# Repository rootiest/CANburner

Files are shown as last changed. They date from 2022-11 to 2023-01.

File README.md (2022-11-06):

# CANBurner

This Project originated from the idea of making the swapping process of the Stealthburner front easier.

CANBurner is a PCB design, that works in cooperation with Hartk's 2pc PCB design.

It consists of a front-part and our adapted CANBurner
The CANBurner is the connection PCB between an EBB36 or EBB42 or any CAN module and the movable front PCB.
over the course of the revisions functions were added and the design was changed. 

# Changelog:
## Rev 1.0 (initial design; tested) 19.10.2022

- adapted the footprint of Hartk's Backplate to fit for our purpose
- JST-XH connectors for 2x fans (Hotend and Part-cooling) and 1x LED added
- 2x3 angled pin header to connect to the front PCB 
- simple wire paths over the board
- a through-hole design for easy soldering at home

first tests by André show, that the design fits perfectly on the CW2 extruder. dimensions reach barely past the motor backplate. 
THD components don't collide with each other or the SB. Functions are fully present and the JST connectors make swapping cables easy.
Space can be used more effectively. JST is not as important, the cables can be soldered directly on the Board.

## Rev 2.0 04.11.2022

- Name CANBurner was suggested by rootiest
- added one more JST-XH for I2C connection
- added 2x4 angled pin header 
- placement of connectors were changed
- added Voron Logo 
- minor cleanup of traces and text

## Rev 2L 05.11.2022

- added Neopixel SMD light as status LED
- changed traces
- added voltage test-points for 24V, 5V and GND
- added "rootiest"-Logo

## Rev 3

- fully changed plug design
- one 8 pin JST-PH to connect to CAN board
- 4 pin socket header to allow for direct I2C connection
- SMD LED and solder traces to skip LED when its ot used

## Credits

CANBurner is a collaboration between [Chris Laprade](https://github.com/rootiest/) and [André Bernbrich](https://github.com/Peviox)

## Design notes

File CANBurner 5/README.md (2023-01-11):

<!--
 Copyright (C) 2022 Chris Laprade (chris@rootiest.com)
 
 This file is part of CANburner.
 
 CANburner is free software: you can redistribute it and/or modify
 it under the terms of the GNU General Public License as published by
 the Free Software Foundation, either version 3 of the License, or
 (at your option) any later version.
 
 CANburner is distributed in the hope that it will be useful,
 but WITHOUT ANY WARRANTY; without even the implied warranty of
 MERCHANTABILITY or FITNESS FOR A PARTICULAR PURPOSE.  See the
 GNU General Public License for more details.
 
 You should have received a copy of the GNU General Public License
 along with CANburner.  If not, see <http://www.gnu.org/licenses/>.
-->

# CANBurner 5

## What is it?

CANBurner is an adaptation of hartk's 2-piece StealthBurner PCB.

CANBurner adapts this concept for use on printers with a CANbus toolhead like the BigTreeTech EBB or the Mellow FLY-SHT.

## What is new in v5?

Version 5 includes all of the features from previous versions.

In addition, v5:

- Fixes an issue with the status LED placement/rotation. It should now be compatible with most common neopixel chips of the appropriate size
  
- Cleans up some trace and mask positioning for better fabrication results

- Adds clearer silkscreen labeling for the LED and Resistor (and accompanying bypasses)

- Re-introduces curvy traces!

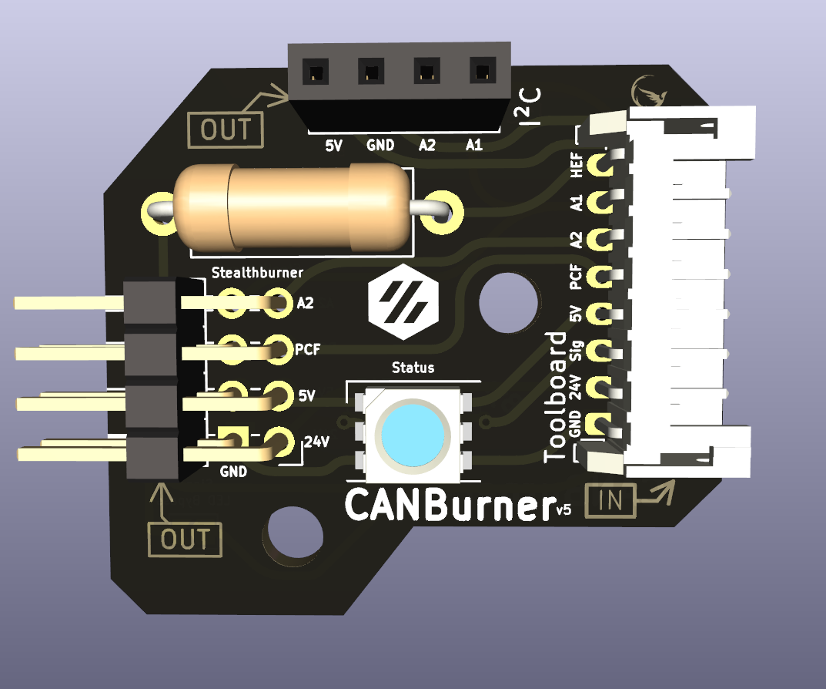
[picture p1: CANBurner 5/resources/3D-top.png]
3D Top View


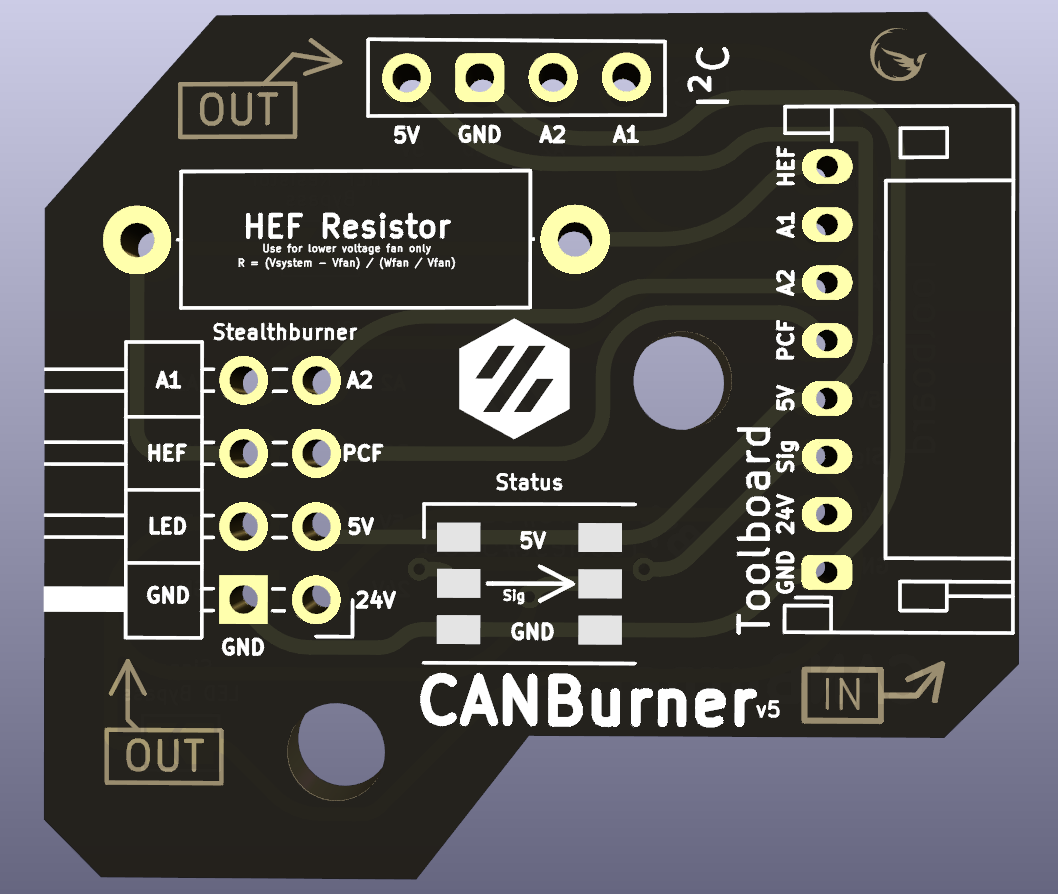
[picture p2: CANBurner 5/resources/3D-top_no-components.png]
3D Top No Components


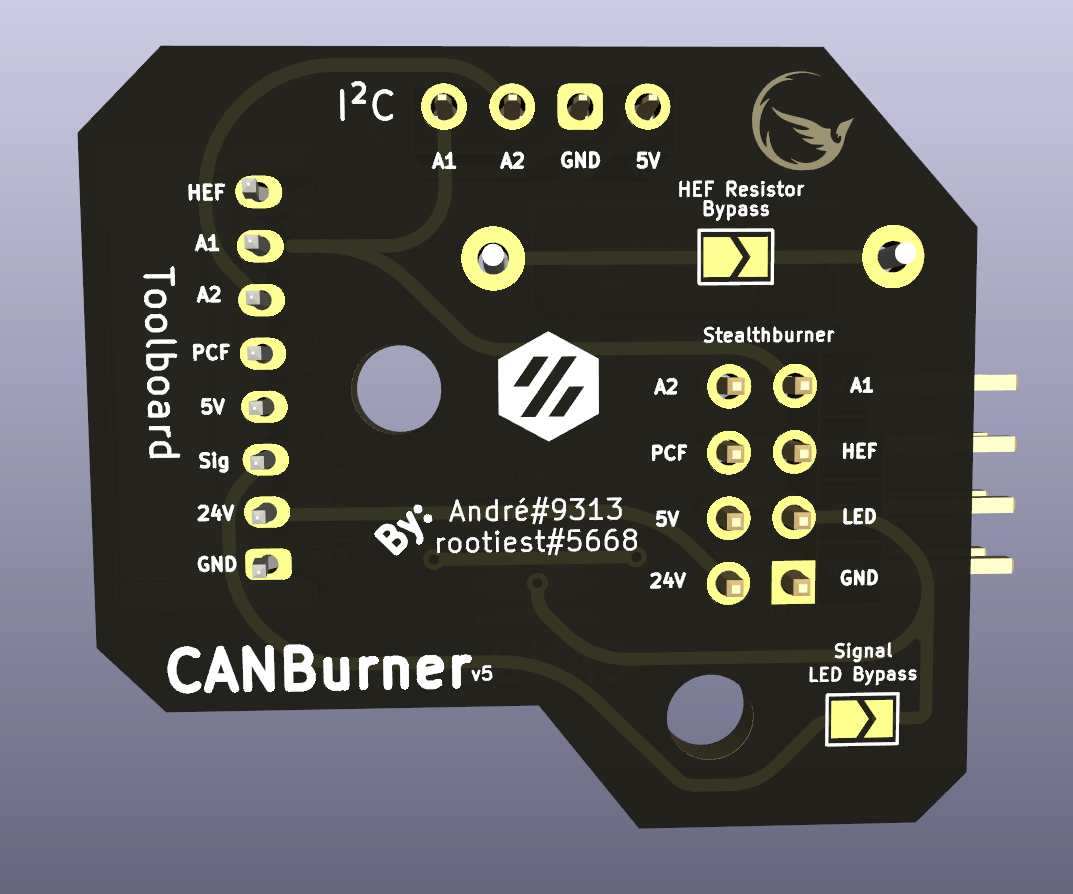
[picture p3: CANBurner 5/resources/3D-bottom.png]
3D Bottom View


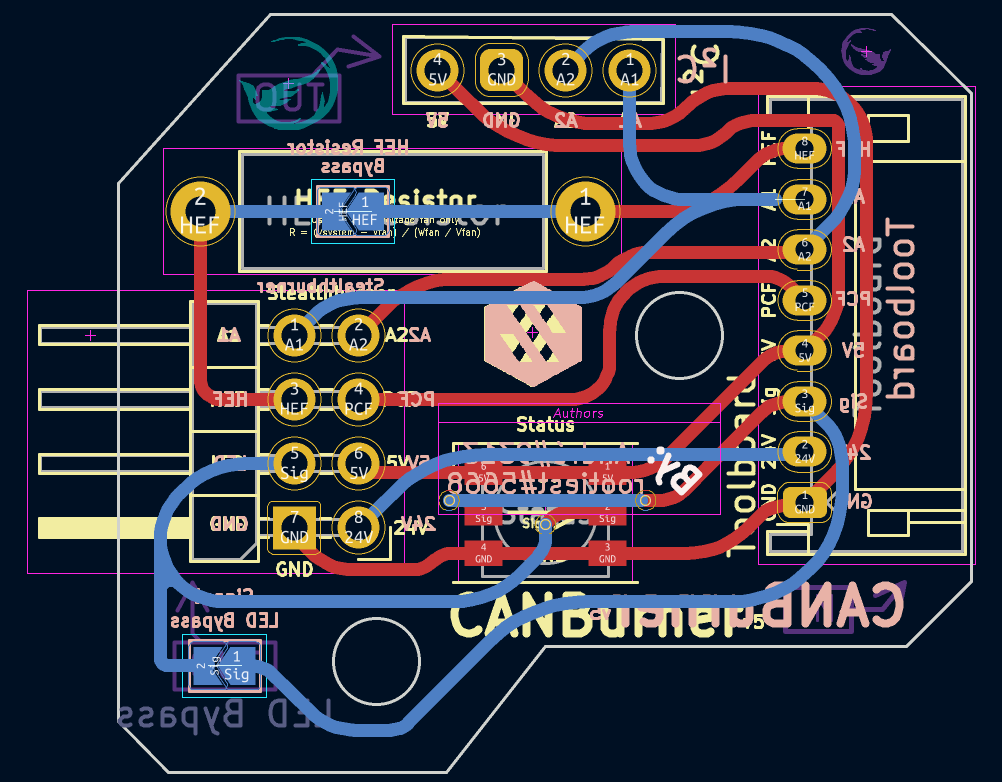
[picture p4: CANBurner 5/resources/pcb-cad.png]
PCB Layout


## How does it work?

Just like [hartk's boards](https://github.com/hartk1213/MISC/tree/main/PCBs/Stealthburner_Toolhead_PCB) do!

[Watch this video](https://www.youtube.com/watch?v=PCIwZRPYMZ8)

Instead of attaching a ribbon, our board just connects to the corresponding pins on your CANbus toolboard.

Its purpose is to act as a "quick-connect" bridge that allows you to remove the stealthburner without disconnecting and reconnecting several connectors for components like fans and LEDs.

The pins will align and connect when you attach the stealthburner front to the extruder.

CANBurner v5 pcb

The images below show an older version but the installation is the same:

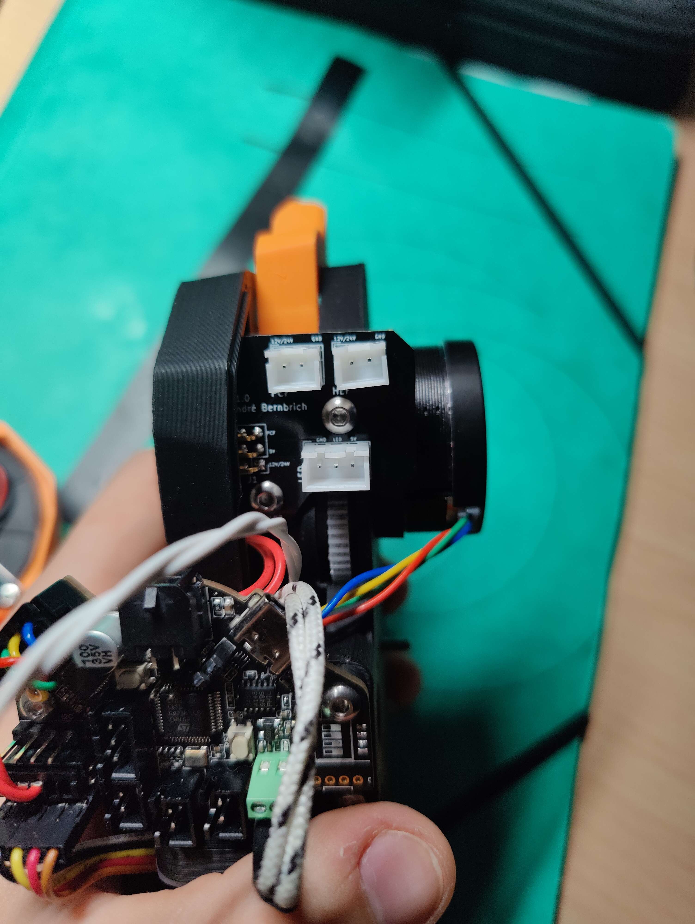
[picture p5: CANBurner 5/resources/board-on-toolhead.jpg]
CANBurner on toolhead


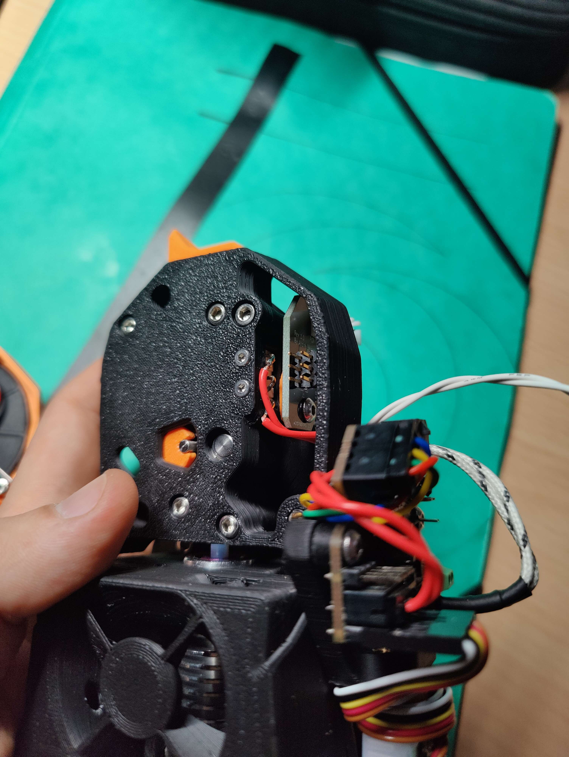
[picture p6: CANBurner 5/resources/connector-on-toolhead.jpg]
CANBurner quick-connect pins


## Credits

CANBurner is a collaboration between [Chris Laprade](https://github.com/rootiest/) and [André Bernbrich](https://github.com/Peviox)

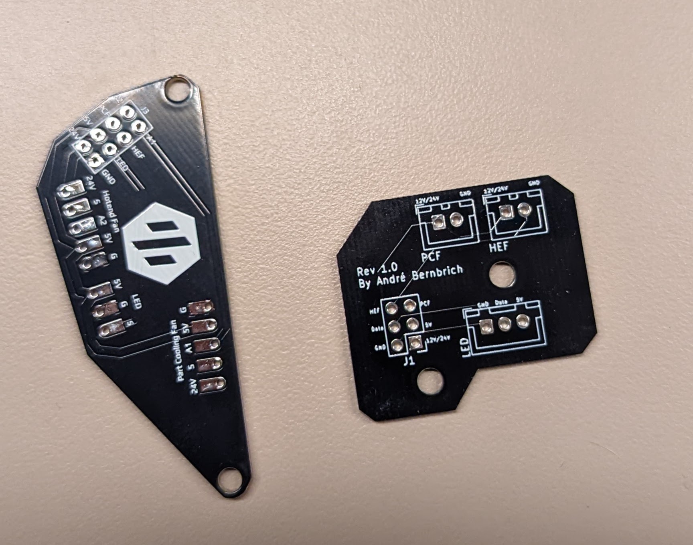
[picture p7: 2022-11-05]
CANBurner 5/resources/pcb-v1.jpg

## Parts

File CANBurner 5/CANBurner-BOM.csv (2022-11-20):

Id | Designator | Package | Quantity | Designation | Supplier and ref
1 | I²C | PinSocket_1x04_P2.54mm_Vertical | 1 | i2C Addon
2 | Status | LED_WS2812_PLCC6_5.0x5.0mm_P1.6mm | 1 | LED_WS2812_PLCC6_5.0x5.0mm_P1.6mm
3 | Toolboard | JST_PH_S8B-PH-K_1x08_P2.00mm_Horizontal | 1 | JST_PH_S8B-PH-K_1x08_P2.00mm_Horizontal
4 | HEF Resistor | R_Axial_DIN0414_L11.9mm_D4.5mm_P15.24mm_Horizontal | 1 | HEF Resistor
5 | J1 | PinHeader_2x04_P2.54mm_Horizontal | 1 | Conn_02x04_Odd_Even

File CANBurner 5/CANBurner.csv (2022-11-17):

Source: | C:\Users\André\Desktop\CANBurner\CANburner\CANBurner 4\SB Quick connect.kicad_sch
Date: | 12.11.2022 12:15:25
Tool: | Eeschema (6.0.8)
Generator: | C:\Program Files\KiCad\6.0\bin\scripting\plugins/bom_csv_grouped_by_value.py
Component Count: | 6
Individual Components:
Item | Qty | Reference(s) | Value | LibPart | Footprint | Datasheet
 |  | HEF1 | Conn_01x02 | Connector_Generic:Conn_01x02 | Connector_JST:JST_XH_B2B-XH-A_1x02_P2.50mm_Vertical | ~
 |  | I2C1 | Conn_01x02 | Connector_Generic:Conn_01x02 | Connector_JST:JST_XH_B2B-XH-A_1x02_P2.50mm_Vertical | ~
 |  | J1 | Conn_02x04_Odd_Even | Connector_Generic:Conn_02x04_Odd_Even | Connector_PinHeader_2.54mm:PinHeader_2x04_P2.54mm_Horizontal | ~
 |  | LED1 | Conn_01x03 | Connector_Generic:Conn_01x03 | Connector_JST:JST_XH_B3B-XH-A_1x03_P2.50mm_Vertical | ~
 |  | PCF1 | Conn_01x02 | Connector_Generic:Conn_01x02 | Connector_JST:JST_XH_B2B-XH-A_1x02_P2.50mm_Vertical | ~
 |  | R1 | R | Device:R | Resistor_THT:R_Axial_DIN0414_L11.9mm_D4.5mm_P15.24mm_Horizontal | ~
Collated Components:
Item | Qty | Reference(s) | Value | LibPart | Footprint | Datasheet
1 | 3 | HEF1, I2C1, PCF1 | Conn_01x02 | Connector_Generic:Conn_01x02 | Connector_JST:JST_XH_B2B-XH-A_1x02_P2.50mm_Vertical | ~
2 | 1 | J1 | Conn_02x04_Odd_Even | Connector_Generic:Conn_02x04_Odd_Even | Connector_PinHeader_2.54mm:PinHeader_2x04_P2.54mm_Horizontal | ~
3 | 1 | LED1 | Conn_01x03 | Connector_Generic:Conn_01x03 | Connector_JST:JST_XH_B3B-XH-A_1x03_P2.50mm_Vertical | ~
4 | 1 | R1 | R | Device:R | Resistor_THT:R_Axial_DIN0414_L11.9mm_D4.5mm_P15.24mm_Horizontal | ~

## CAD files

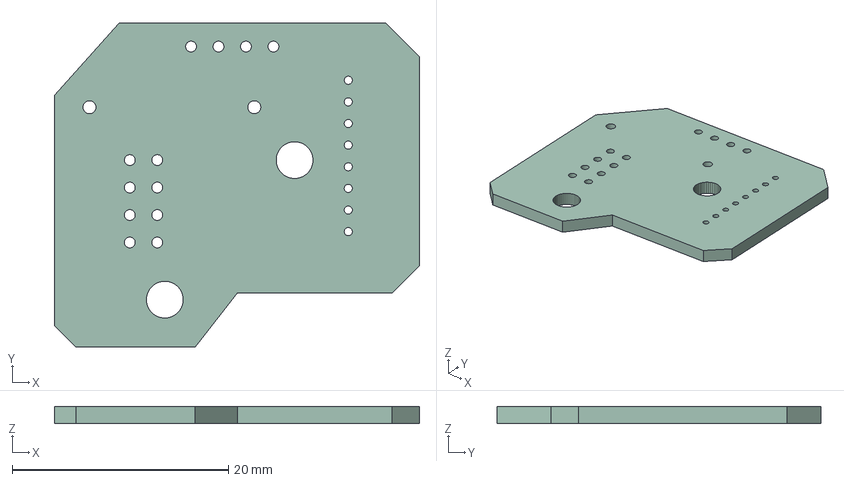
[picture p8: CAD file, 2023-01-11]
CANBurner 5/CANBurner.step
33.8 x 30.0 x 1.58 mm

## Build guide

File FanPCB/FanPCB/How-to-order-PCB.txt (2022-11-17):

How to Order PCB

Please refer to:
https://docs.easyeda.com/en/PCB/Order-PCB

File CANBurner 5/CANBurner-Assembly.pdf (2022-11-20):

# 5V GND

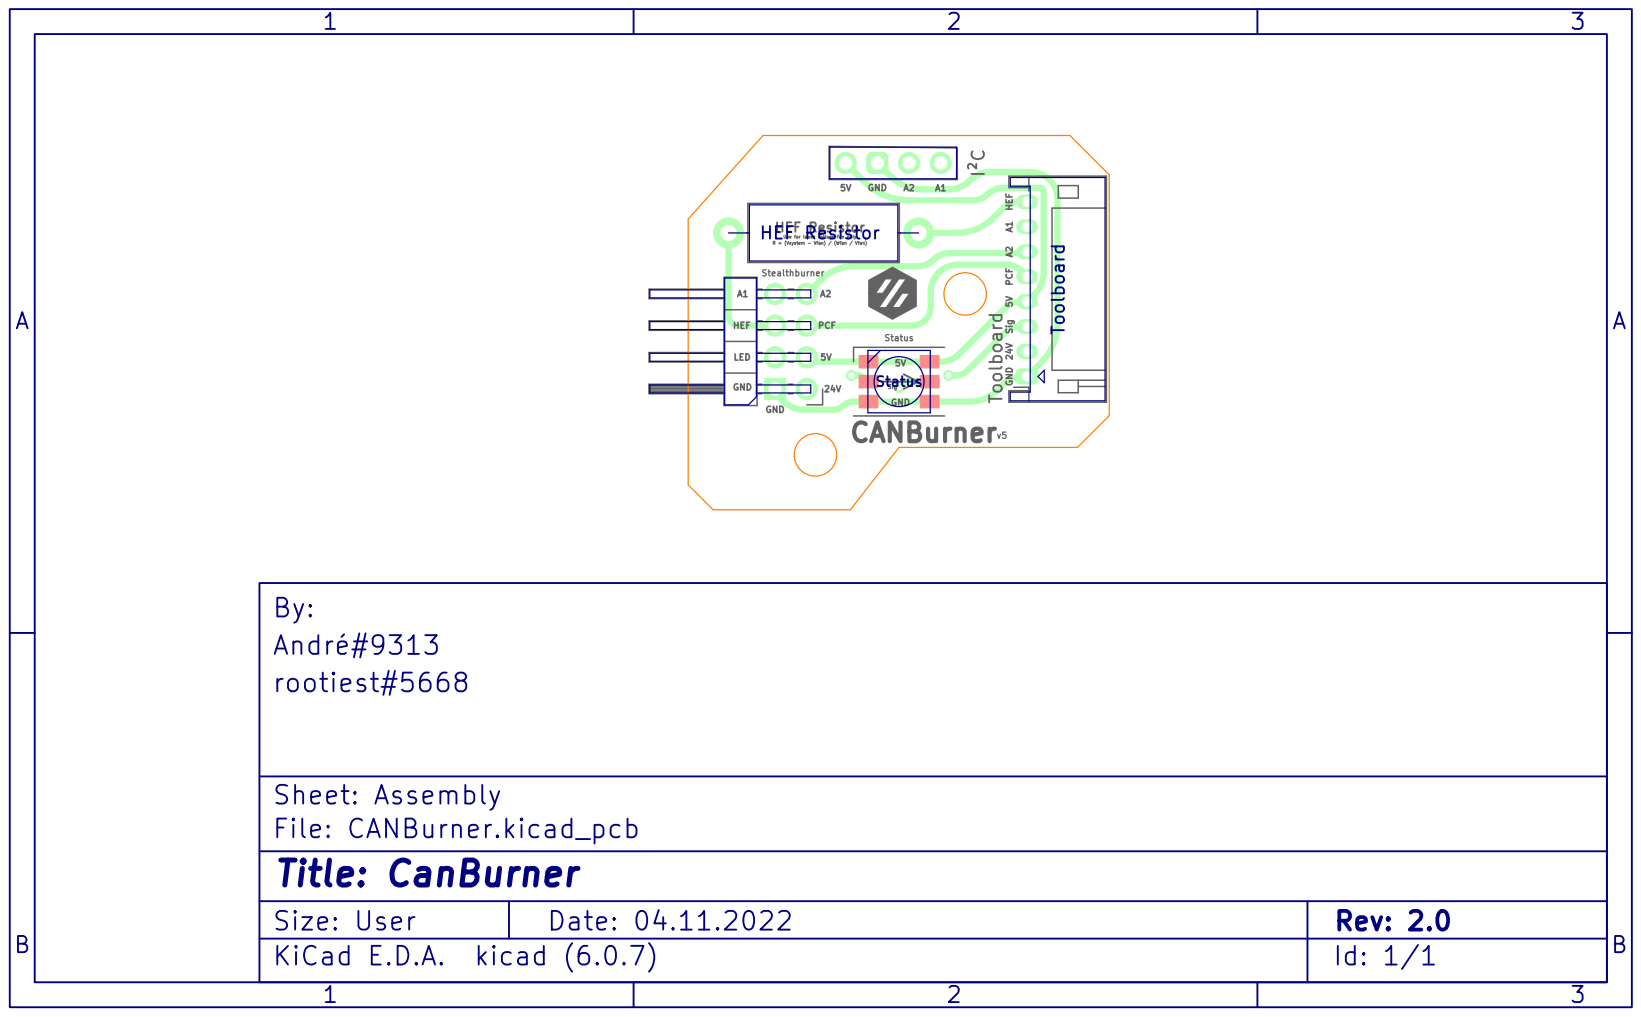
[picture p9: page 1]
GND CANBurner; Sig GND; PCF; Use for lower voltage fan only LED; 24V HEF A1; HEF Resistor; A¹ GND; A2 Stealthburner; PCF A² I²C; Status; Toolboard 1; B Date: 04.11.2022 KiCad E.D.A. kicad (6.0.7) Size: User; Rev: 2.0; rootiest#5668 André#9313 By:; Toolboard HEF Resistor

R = (Vsystem - Vfan) / (Wfan / Vfan) HEF

Sheet: Assembly
File: CANBurner.kicad_pcb
Id: 1/1 Title: CanBurner

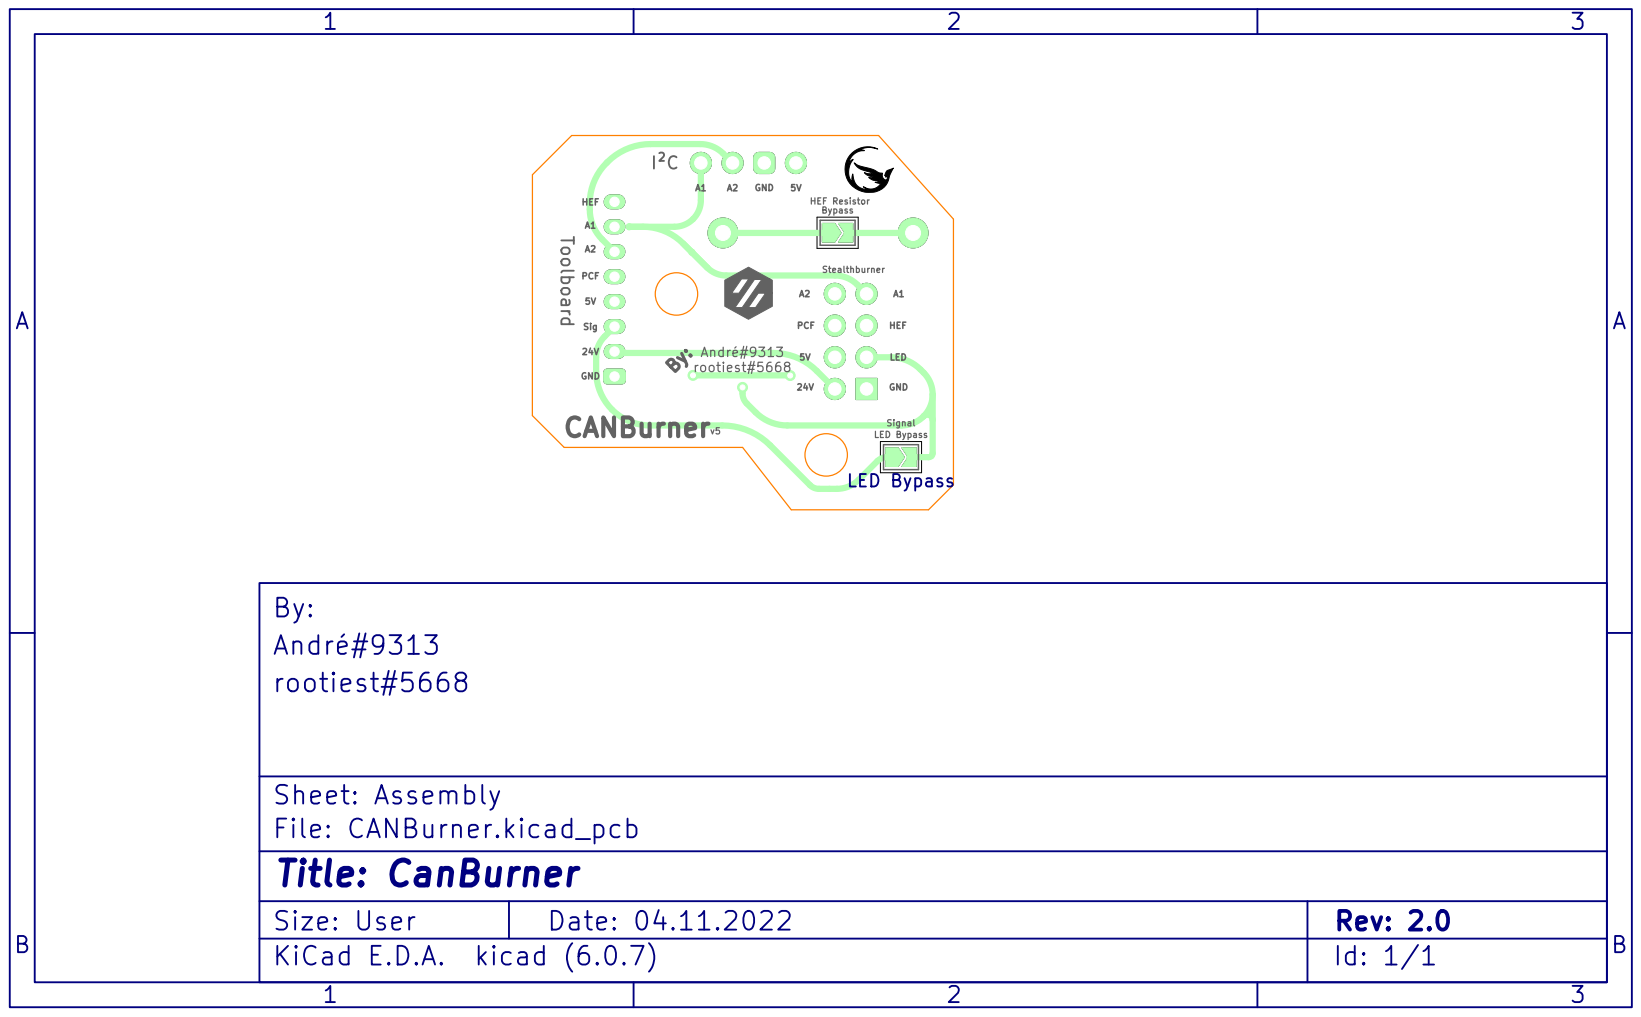
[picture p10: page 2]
v5 HEF; HEF A1; I²C; 24V GND; GND; Stealthburner A1; Signal A2 Toolboard; Sig; PCF CANBurner; HEF Resistor; GND André#9313; rootiest#5668; PCF; LED By:; Bypass; LED Bypass 1; B Date: 04.11.2022 KiCad E.D.A. kicad (6.0.7) Size: User; Rev: 2.0; rootiest#5668 André#9313 By:; LED Bypass

Sheet: Assembly
File: CANBurner.kicad_pcb
Id: 1/1 Title: CanBurner

# 5V GND

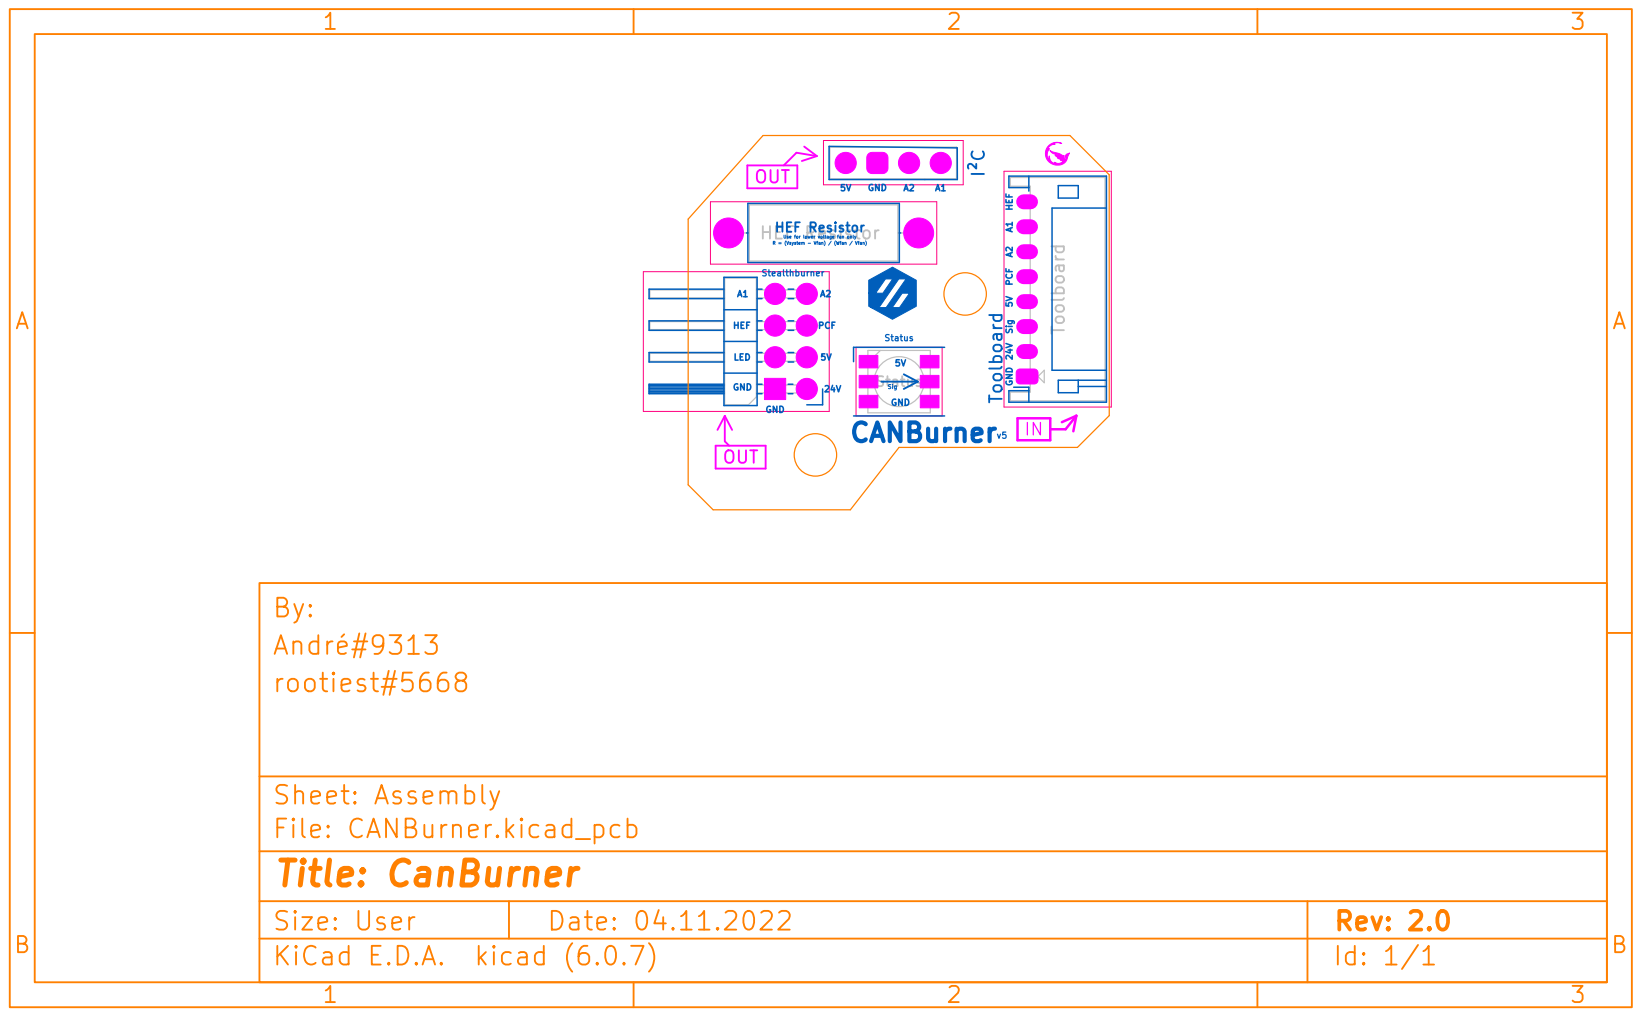
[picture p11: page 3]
Status; Toolboard HEF Resistor OUTOUT; GND CANBurner; Sig GND; PCF; Use for lower voltage fan only LED; 24V HEF A1; HEF Resistor; A¹ GND; A2 Stealthburner; PCF A² I²C; Toolboard 1; B Date: 04.11.2022 KiCad E.D.A. kicad (6.0.7) Size: User; Rev: 2.0

R = (Vsystem - Vfan) / (Wfan / Vfan) HEF

rootiest#5668 André#9313 By:

Sheet: Assembly
File: CANBurner.kicad_pcb
Id: 1/1 Title: CanBurner

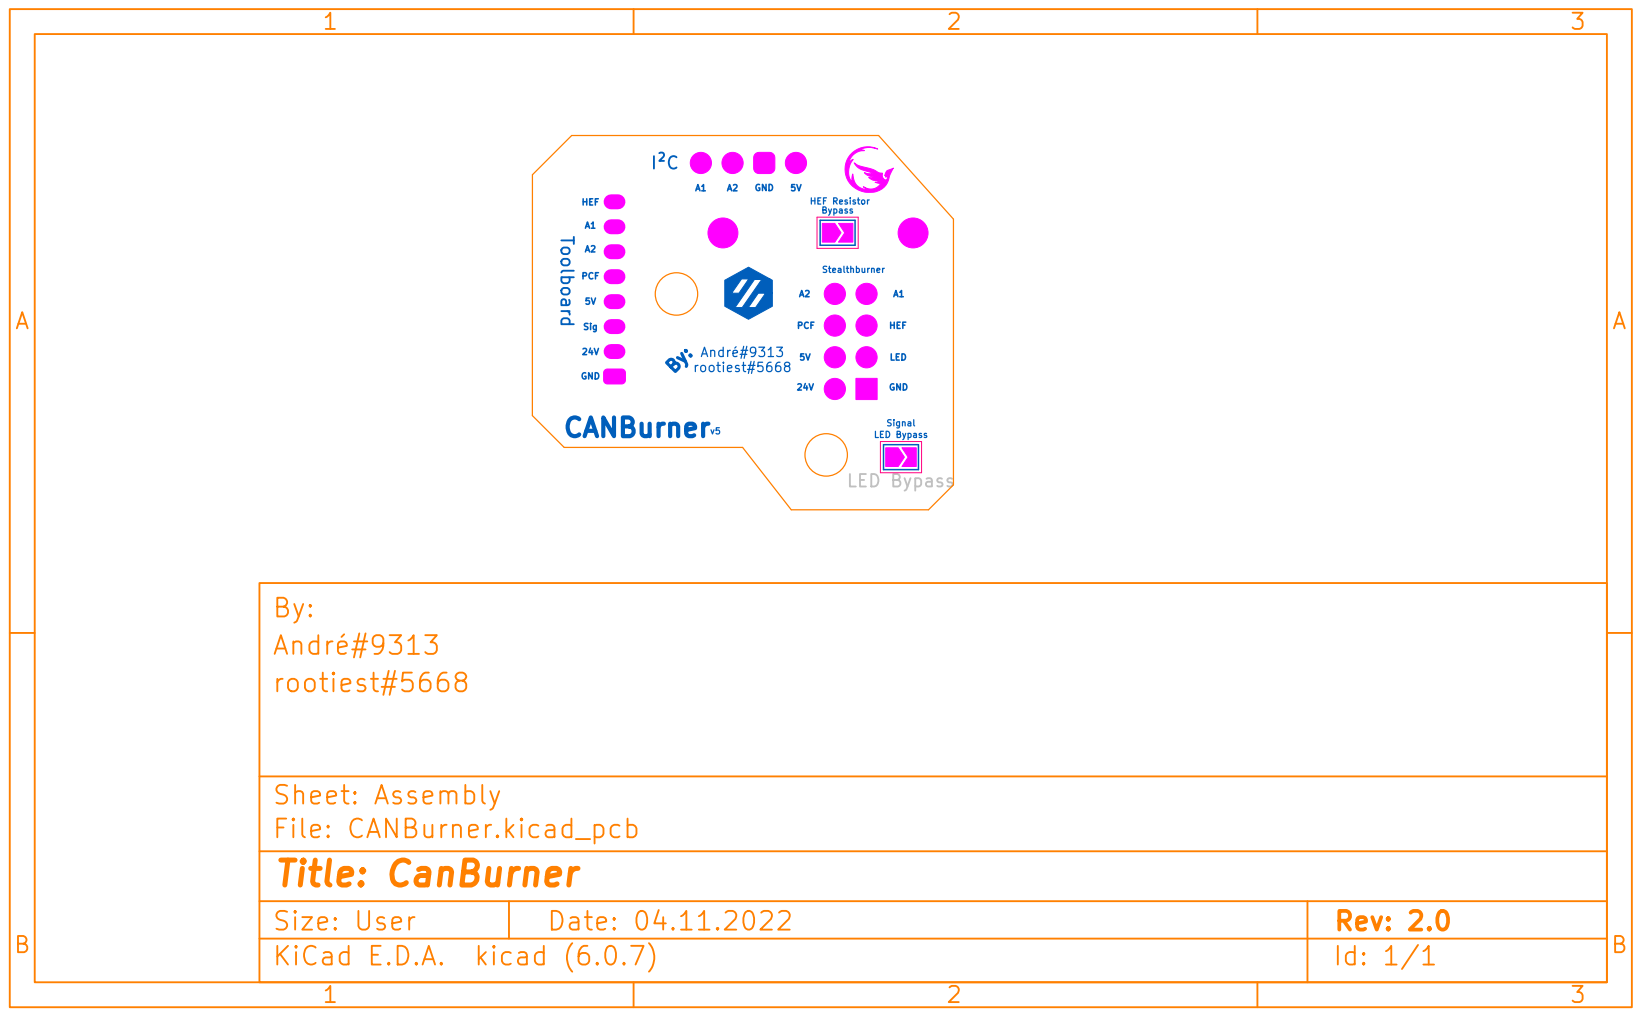
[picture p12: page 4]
LED Bypass; v5 HEF; HEF A1; I²C; 24V GND; GND; Stealthburner A1; Signal A2 Toolboard; Sig; PCF CANBurner; HEF Resistor; GND André#9313; rootiest#5668; PCF; LED By:; Bypass; LED Bypass 1; B Date: 04.11.2022 KiCad E.D.A. kicad (6.0.7) Size: User; Rev: 2.0

rootiest#5668 André#9313 By:

Sheet: Assembly
File: CANBurner.kicad_pcb
Id: 1/1 Title: CanBurner

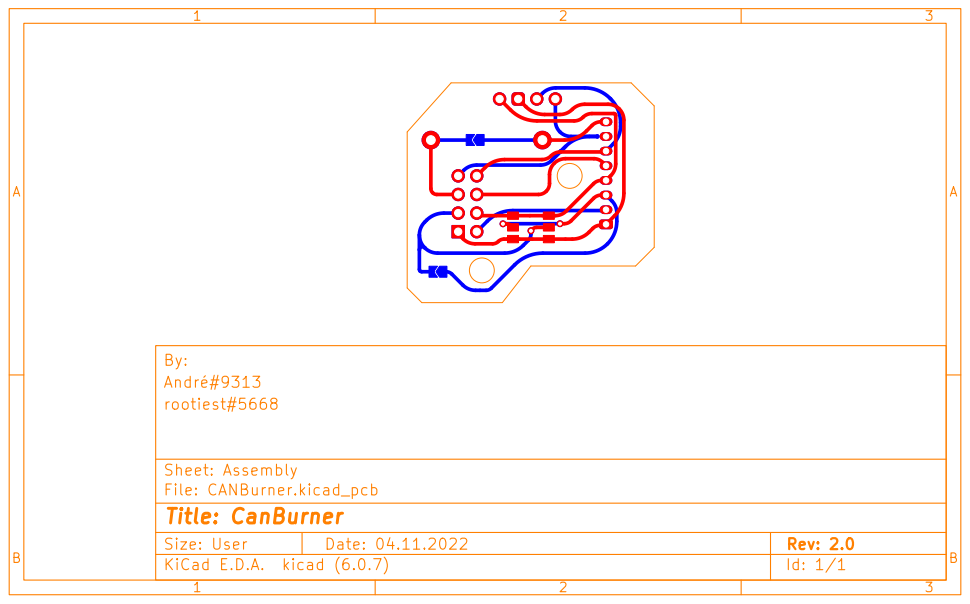
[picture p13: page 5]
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

rootiest#5668 André#9313 By:

Sheet: Assembly
File: CANBurner.kicad_pcb
Id: 1/1 Title: CanBurner

# 5V GND

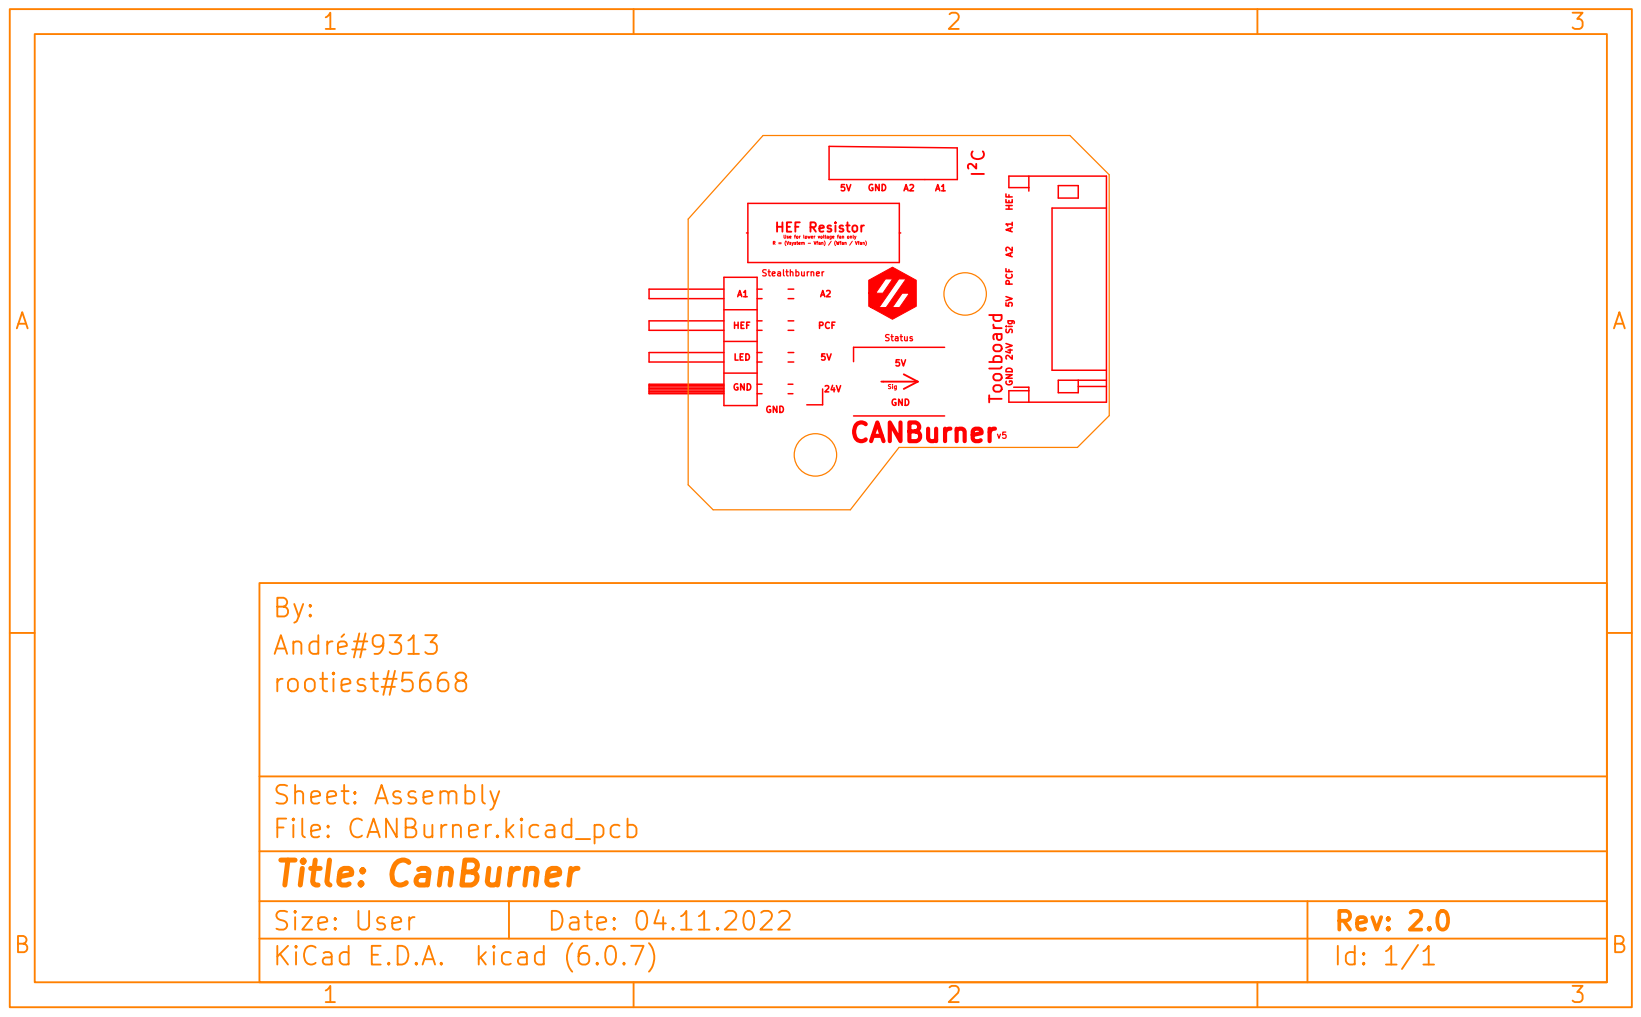
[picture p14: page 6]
GND CANBurner; Sig GND; PCF; Use for lower voltage fan only LED; 24V HEF A1; HEF Resistor; A¹ GND; A2 Stealthburner; PCF A² I²C; Status; Toolboard 1; B Date: 04.11.2022 KiCad E.D.A. kicad (6.0.7) Size: User; Rev: 2.0

R = (Vsystem - Vfan) / (Wfan / Vfan) HEF

rootiest#5668 André#9313 By:

Sheet: Assembly
File: CANBurner.kicad_pcb
Id: 1/1 Title: CanBurner

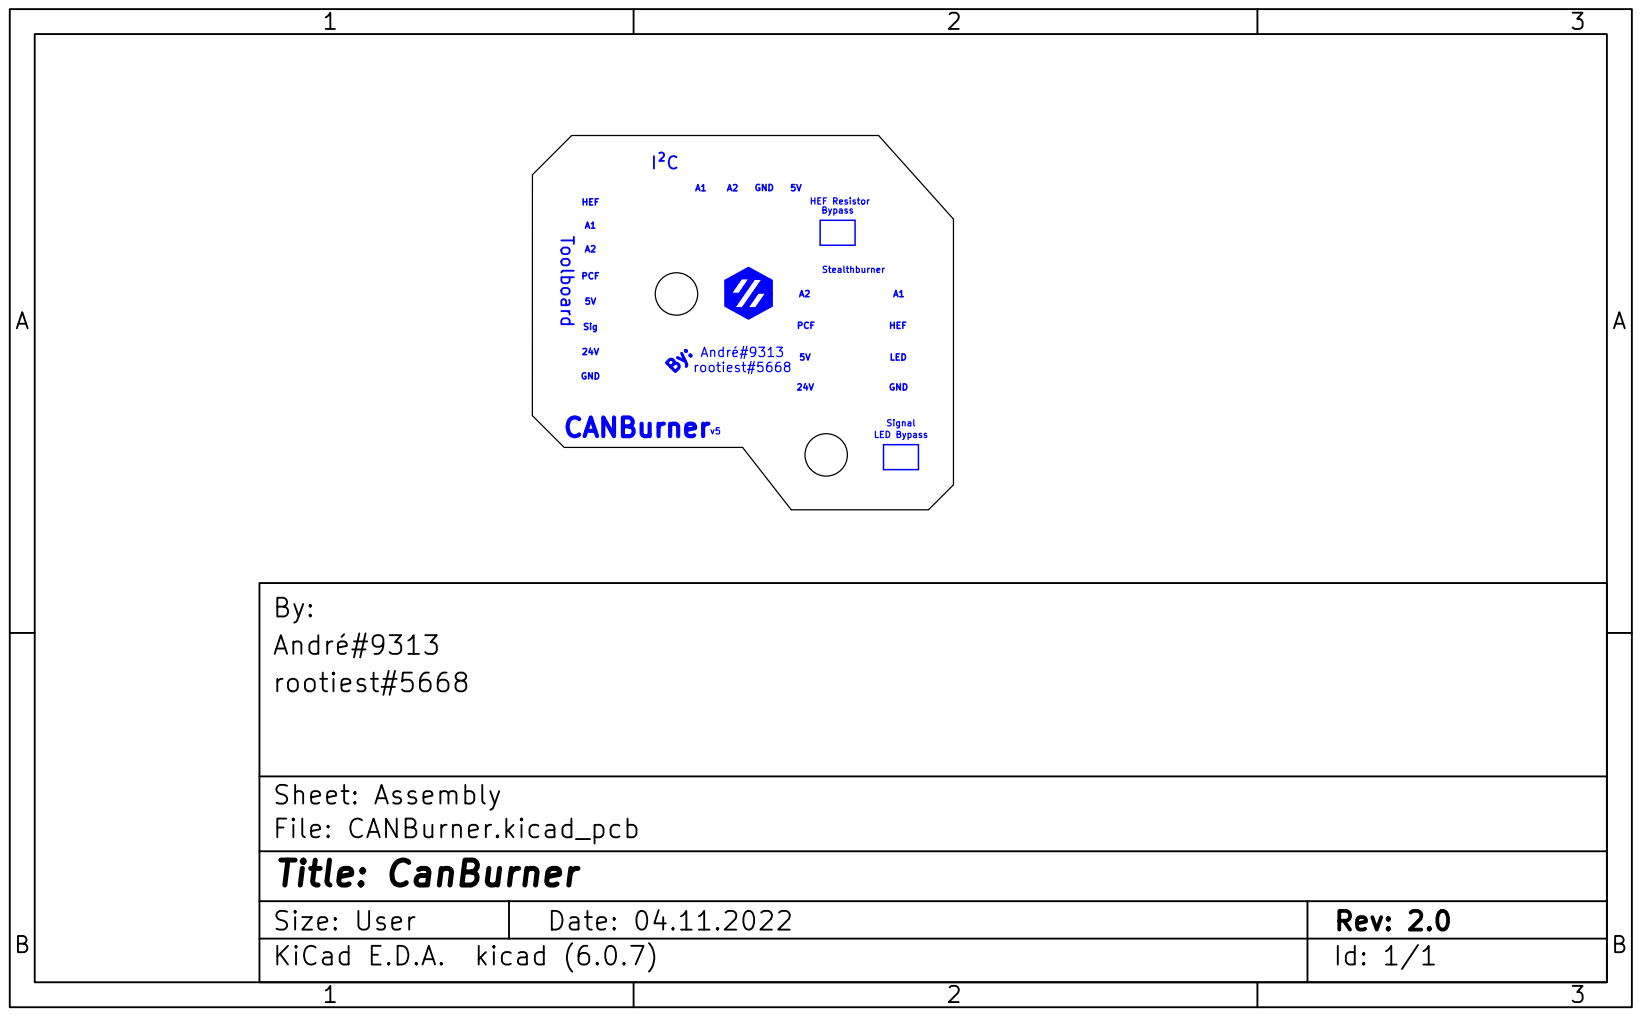
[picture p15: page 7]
v5 HEF; HEF A1; I²C; 24V GND; GND; Stealthburner A1; Signal A2 Toolboard; Sig; PCF CANBurner; HEF Resistor; GND André#9313; rootiest#5668; PCF; LED By:; Bypass; LED Bypass 1; B Date: 04.11.2022 KiCad E.D.A. kicad (6.0.7) Size: User; Rev: 2.0

rootiest#5668 André#9313 By:

Sheet: Assembly
File: CANBurner.kicad_pcb
Id: 1/1 Title: CanBurner

# OUTOUT

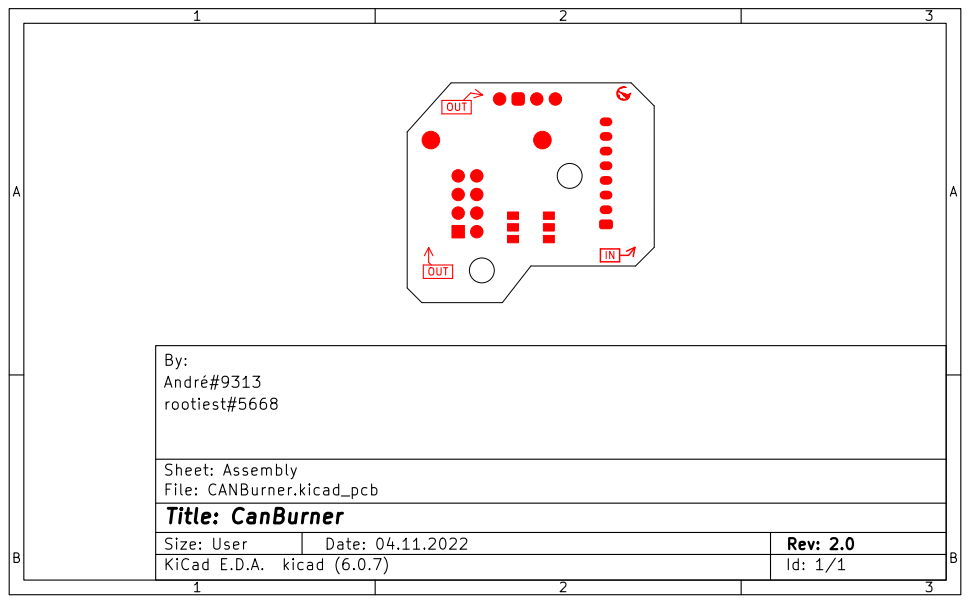
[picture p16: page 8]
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

rootiest#5668 André#9313 By:

Sheet: Assembly
File: CANBurner.kicad_pcb
Id: 1/1 Title: CanBurner

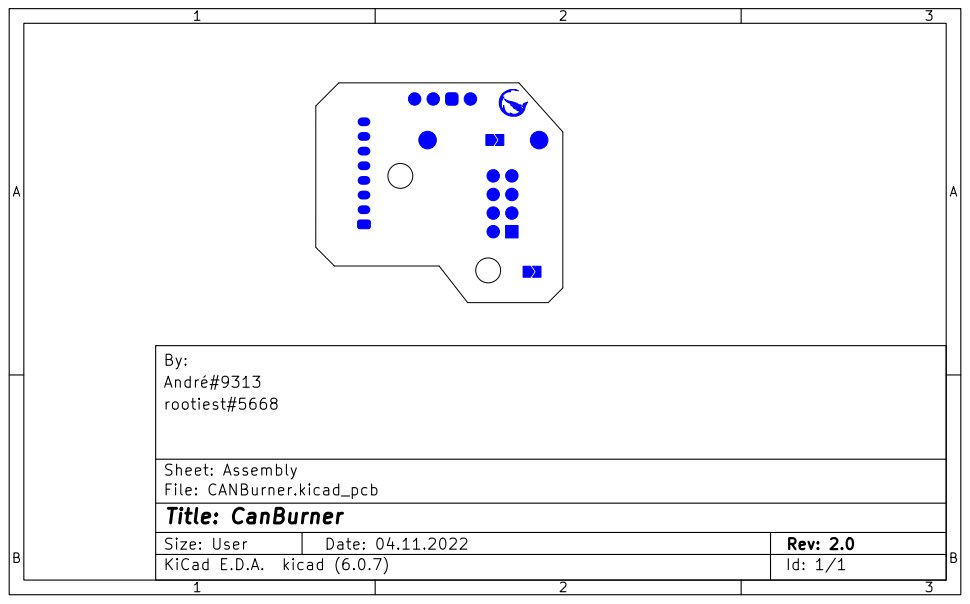
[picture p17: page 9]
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

rootiest#5668 André#9313 By:

Sheet: Assembly
File: CANBurner.kicad_pcb
Id: 1/1 Title: CanBurner

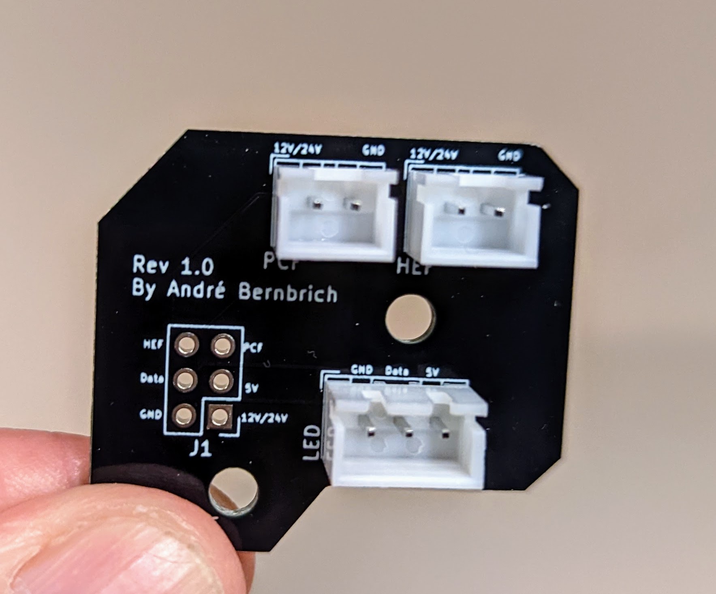
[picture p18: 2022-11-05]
CANBurner 5/resources/pcb-v1-soldered.jpg

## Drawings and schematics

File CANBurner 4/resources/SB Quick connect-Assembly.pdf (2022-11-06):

# 5V GND

## A2 GND CANBurner

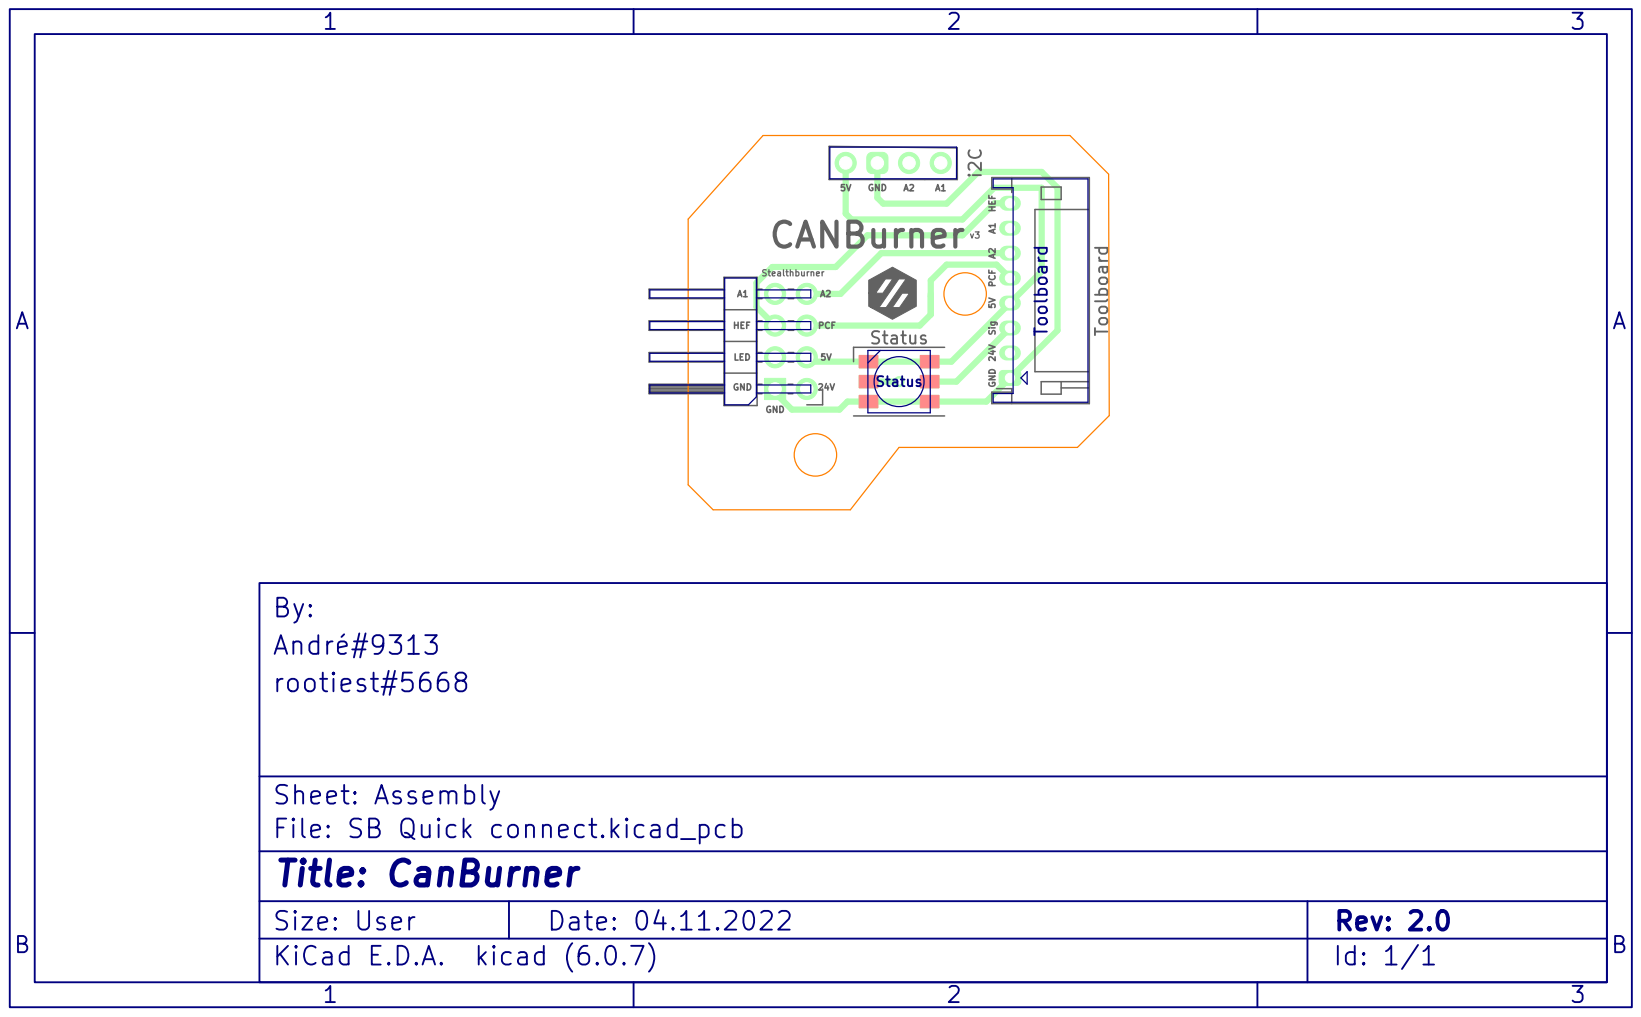
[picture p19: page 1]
GND; PCF; LED; SigHEF; 24V HEF A1; A¹ GND; A2 Stealthburner; PCF A² i2C; Status; Toolboard 1; B Date: 04.11.2022 KiCad E.D.A. kicad (6.0.7) Size: User; Rev: 2.0; rootiest#5668 André#9313 By:; Toolboard

Sheet: Assembly
File: SB Quick connect.kicad_pcb
Id: 1/1 Title: CanBurner

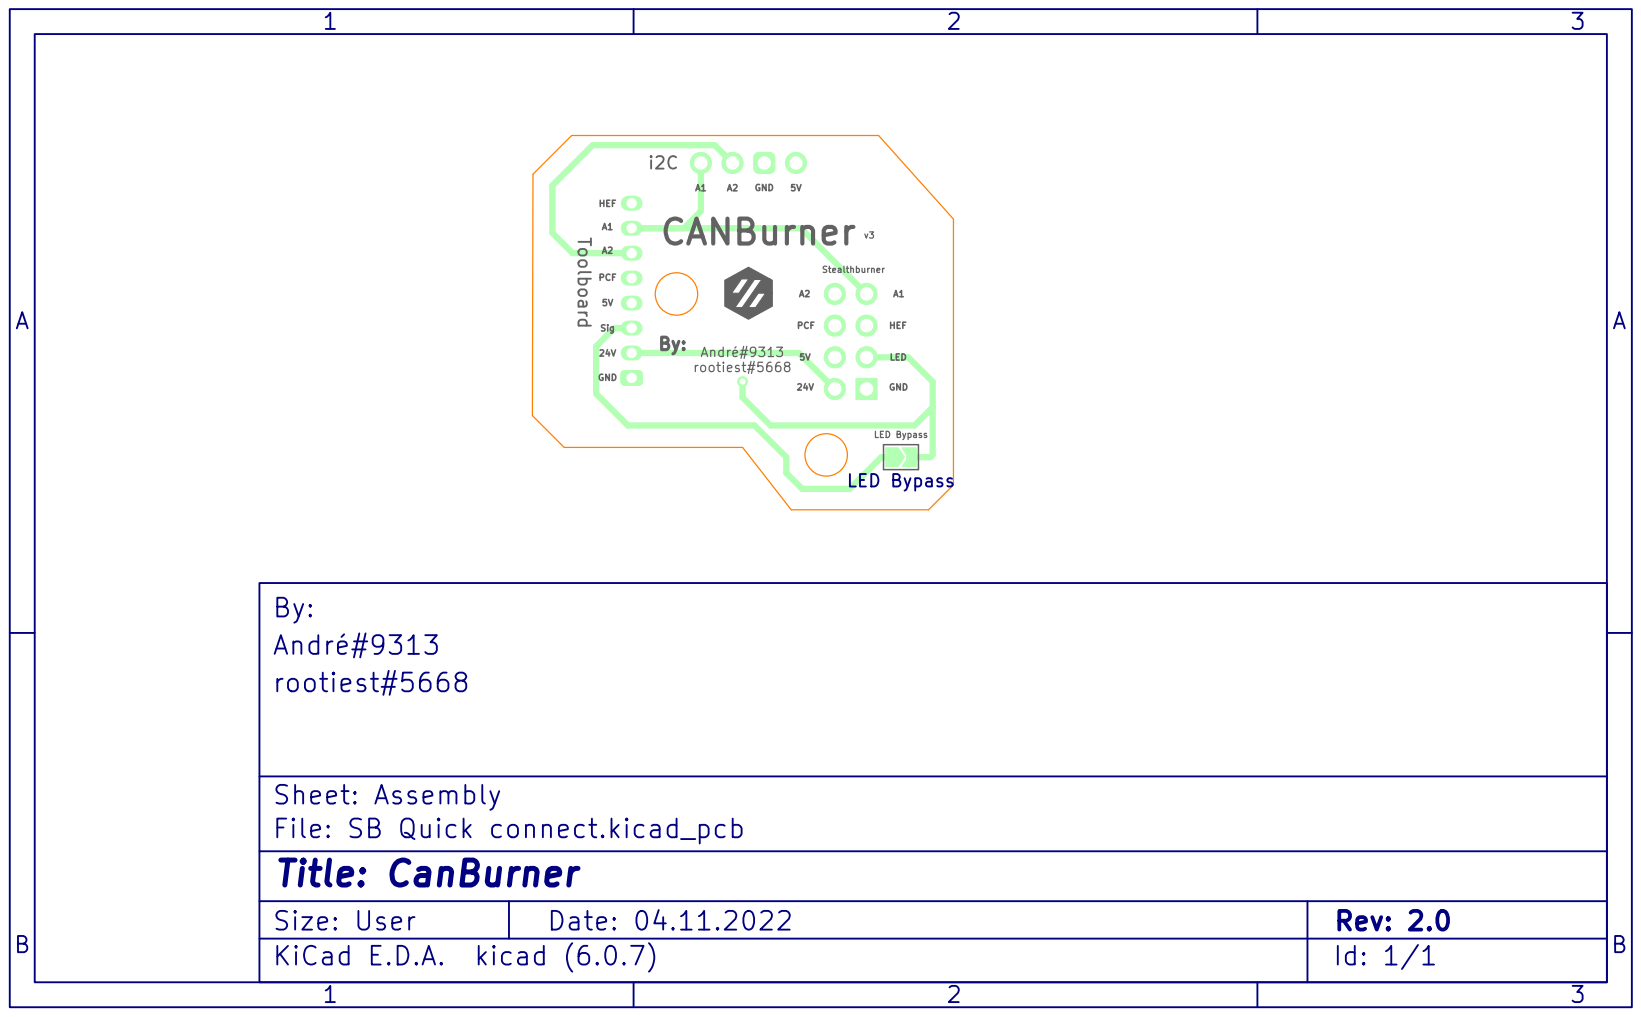
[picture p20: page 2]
v3 HEF; HEF A1; 24V GND; GND; Stealthburner A1; A2 Toolboard; Sig; PCF CANBurner; GND André#9313 rootiest#5668; PCF; LED By:; LED Bypass 1; B Date: 04.11.2022 KiCad E.D.A. kicad (6.0.7) Size: User; Rev: 2.0; rootiest#5668 André#9313 By:; LED Bypass

Sheet: Assembly
File: SB Quick connect.kicad_pcb
Id: 1/1 Title: CanBurner

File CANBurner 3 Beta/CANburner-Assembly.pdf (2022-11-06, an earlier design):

# 5V GND

## A2 GND CANBurner

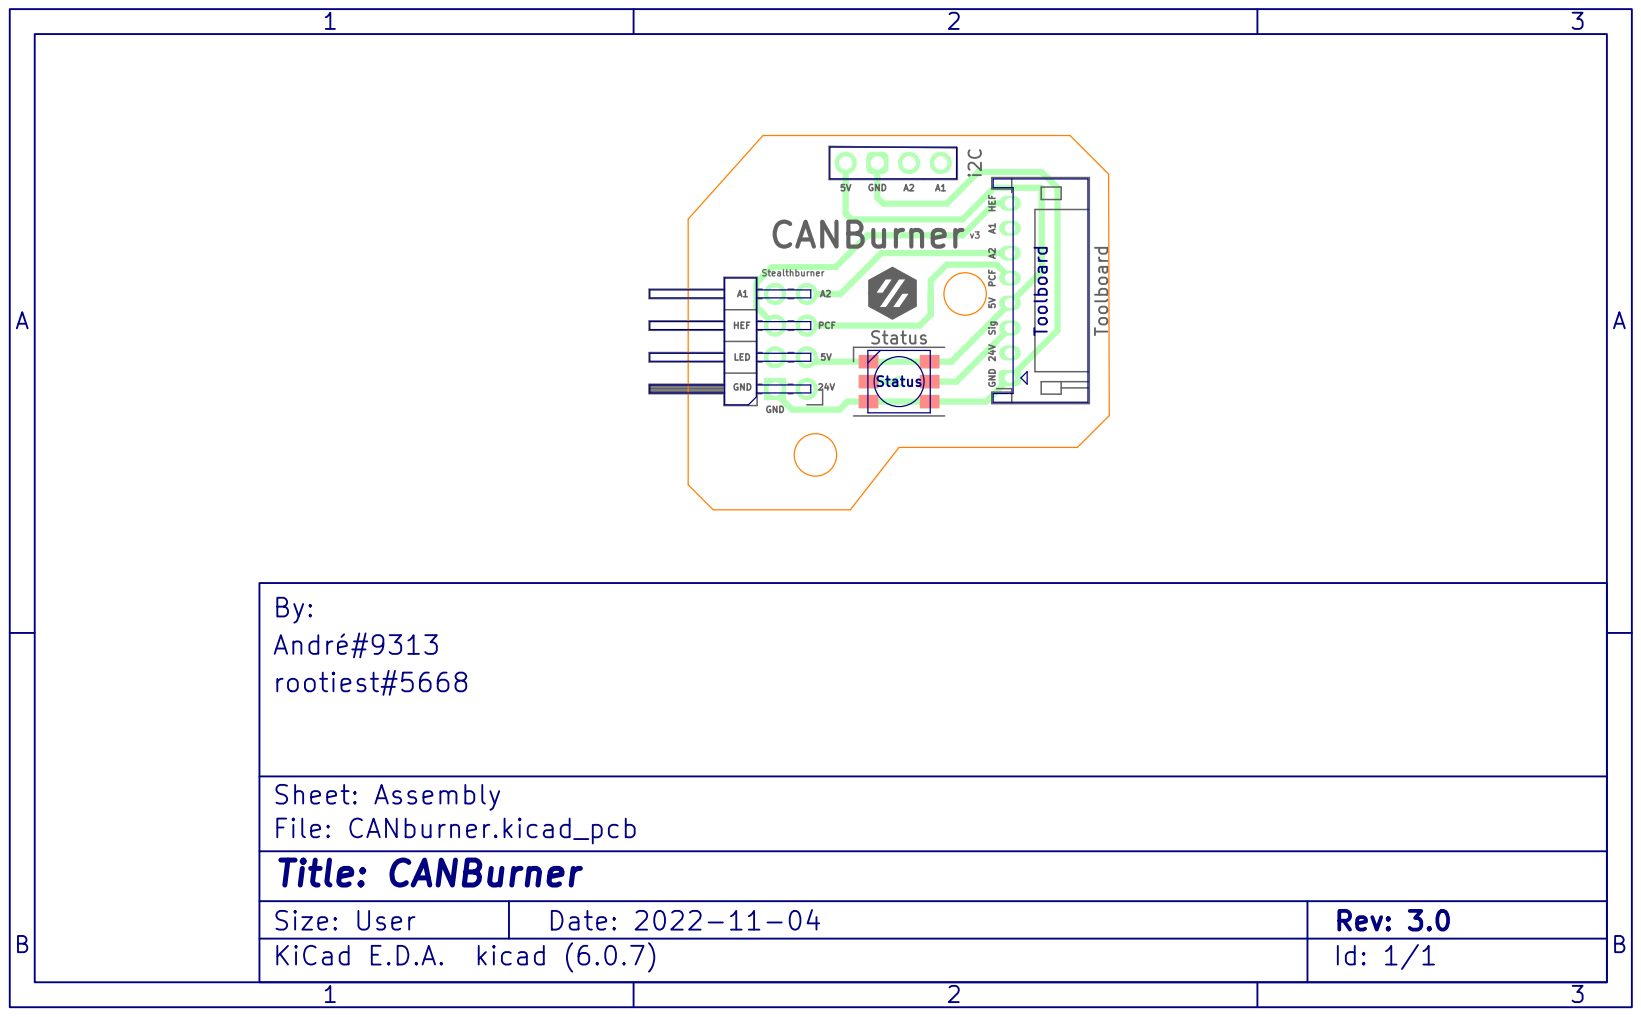
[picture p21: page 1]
GND; PCF; LED; SigHEF; 24V HEF A1; A¹ GND; A2 Stealthburner; PCF A² i2C; Status; Toolboard 1; B Date: 2022-11-04 KiCad E.D.A. kicad (6.0.7) Size: User; Rev: 3.0; rootiest#5668 André#9313 By:; Toolboard

Sheet: Assembly
File: CANburner.kicad_pcb
Id: 1/1 Title: CANBurner

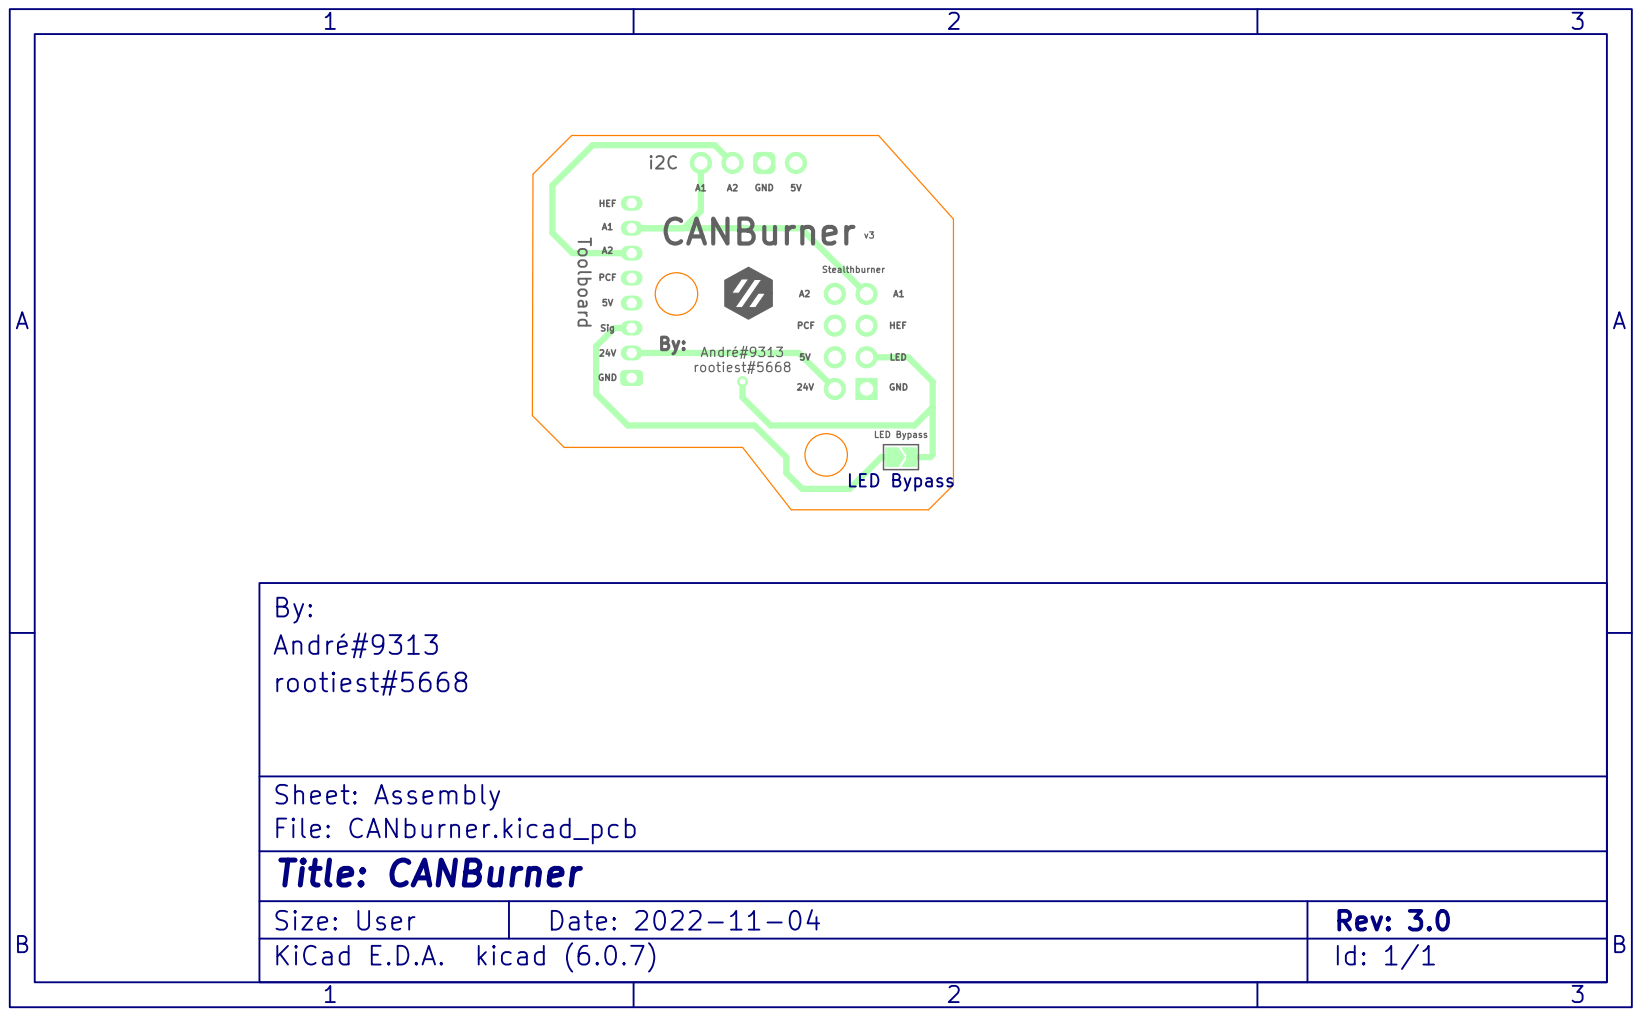
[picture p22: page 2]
v3 HEF; HEF A1; 24V GND; GND; Stealthburner A1; A2 Toolboard; Sig; PCF CANBurner; GND André#9313 rootiest#5668; PCF; LED By:; LED Bypass 1; B Date: 2022-11-04 KiCad E.D.A. kicad (6.0.7) Size: User; Rev: 3.0; rootiest#5668 André#9313 By:; LED Bypass

Sheet: Assembly
File: CANburner.kicad_pcb
Id: 1/1 Title: CANBurner

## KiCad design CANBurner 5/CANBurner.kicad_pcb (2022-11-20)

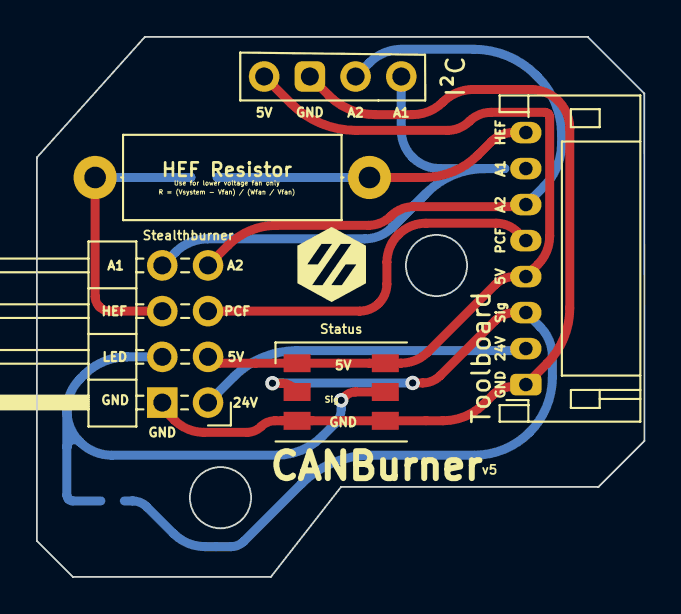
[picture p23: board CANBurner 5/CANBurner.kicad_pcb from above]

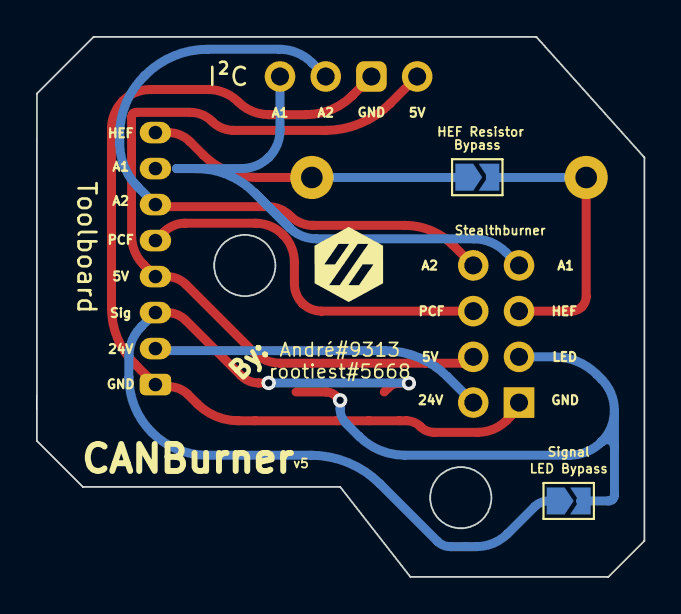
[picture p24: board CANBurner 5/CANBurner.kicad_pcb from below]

Board: 2 copper layers, 33.8 x 30.0 mm, 7 parts (2 on the bottom side), 8 nets.

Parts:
Bypass: LED Bypass; SolderJumper-2_P1.3mm_Open_TrianglePad1.0x1.5mm
HEF Resistor: HEF Resistor; R_Axial_DIN0414_L11.9mm_D4.5mm_P15.24mm_Horizontal
I²C: i2C Addon; PinSocket_1x04_P2.54mm_Vertical
J1: Conn_02x04_Odd_Even; PinHeader_2x04_P2.54mm_Horizontal
LED Bypass: LED Bypass; SolderJumper-2_P1.3mm_Open_TrianglePad1.0x1.5mm
Status: LED_WS2812_PLCC6_5.0x5.0mm_P1.6mm
Toolboard: JST_PH_S8B-PH-K_1x08_P2.00mm_Horizontal

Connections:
/5V: I²C.4, J1.6, Status.1, Status.6, Toolboard.4
/24V: J1.8, Toolboard.2
/A1: I²C.1, J1.1, Toolboard.7
/A2: I²C.2, J1.2, Toolboard.6
/GND: I²C.3, J1.7, Status.3, Status.4, Toolboard.1
/HEF: Bypass.1, Bypass.2, HEF Resistor.1, HEF Resistor.2, J1.3, Toolboard.8
/PCF: J1.4, Toolboard.5
/Sig: J1.5, LED Bypass.1, LED Bypass.2, Status.2, Status.5, Toolboard.3

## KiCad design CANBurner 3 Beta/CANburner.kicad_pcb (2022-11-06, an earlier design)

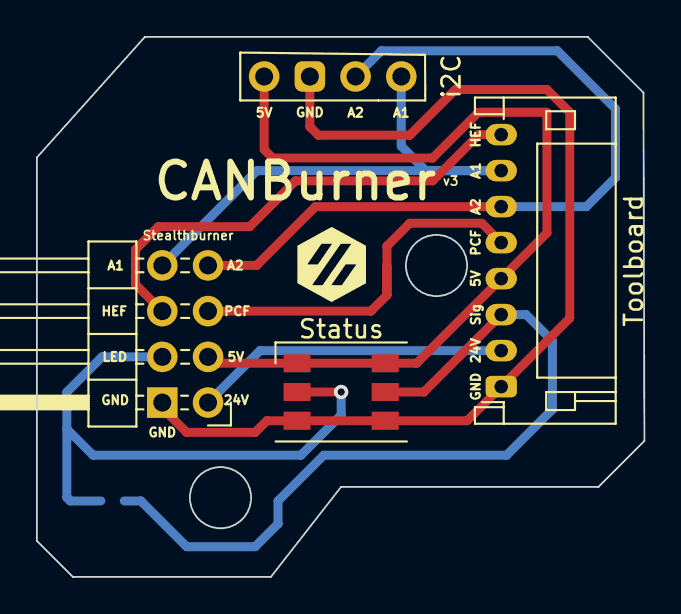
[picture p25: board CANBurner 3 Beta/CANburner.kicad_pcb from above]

Board: 2 copper layers, 33.8 x 30.0 mm, 5 parts (1 on the bottom side), 8 nets.

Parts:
LED Bypass: LED Bypass; SolderJumper-2_P1.3mm_Open_TrianglePad1.0x1.5mm
Status: LED_WS2812_PLCC6_5.0x5.0mm_P1.6mm
Stealthburner: Conn_02x04_Odd_Even; PinHeader_2x04_P2.54mm_Horizontal
Toolboard: JST_PH_S8B-PH-K_1x08_P2.00mm_Horizontal
i2C: i2C Addon; PinSocket_1x04_P2.54mm_Vertical

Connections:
/5V: Status.1, Status.6, Stealthburner.6, Toolboard.4, i2C.4
/24V: Stealthburner.8, Toolboard.2
/A1: Stealthburner.1, Toolboard.7, i2C.1
/A2: Stealthburner.2, Toolboard.6, i2C.2
/GND: Status.3, Status.4, Stealthburner.7, Toolboard.1, i2C.3
/HEF: Stealthburner.3, Toolboard.8
/PCF: Stealthburner.4, Toolboard.5
/Sig: LED Bypass.1, LED Bypass.2, Status.2, Status.5, Stealthburner.5, Toolboard.3

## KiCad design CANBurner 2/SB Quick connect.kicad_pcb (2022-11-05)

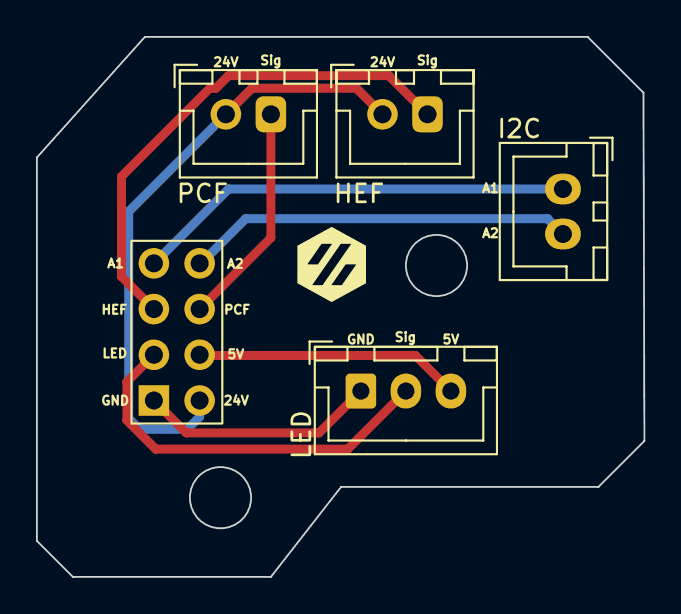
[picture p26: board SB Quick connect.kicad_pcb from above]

Board: 2 copper layers, 33.8 x 30.0 mm, 5 parts (0 on the bottom side), 8 nets.

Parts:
HEF: Conn_01x02; JST_XH_B2B-XH-A_1x02_P2.50mm_Vertical
I2C: Conn_01x02; JST_XH_B2B-XH-A_1x02_P2.50mm_Vertical
J1: Conn_02x04_Odd_Even; PinHeader_2x04_P2.54mm_Vertical
LED: Conn_01x03; JST_XH_B3B-XH-A_1x03_P2.50mm_Vertical
PCF: Conn_01x02; JST_XH_B2B-XH-A_1x02_P2.50mm_Vertical

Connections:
/5V: J1.6, LED.3
/24V: HEF.1, J1.8, PCF.1
/A1: I2C.1, J1.1
/A2: I2C.2, J1.2
/GND: J1.7, LED.1
/HEF: HEF.2, J1.3
/PCF: J1.4, PCF.2
/Sig: J1.5, LED.2

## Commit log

2022-11-05 Create separate folder for version 2L
    [SB Quick connect.csv, SB Quick connect.kicad_pcb, SB Quick connect.kicad_sch]
2022-11-05 Add CANBurner 2 directory
    [SB Quick connect.csv, SB Quick connect.kicad_pcb, SB Quick connect.kicad_sch]
2022-11-06 CANBurner 3 Beta
    [SB Quick connect.csv, SB Quick connect.kicad_pcb, SB Quick connect.kicad_sch]
2022-11-06 Modified pin order on i2c header
    Now fits better with the order most breakouts use.
    [SB Quick connect.kicad_pcb]
2022-11-06 Assembly Blueprints
2022-11-06 Minor adjustments to LED Signal tracks
    Moved tracks further from edges/mounting screws
    [SB Quick connect.kicad_pcb]
2022-11-06 Another LED Signal Track tweak
    Slightly adjusted the tracks on the bypass pad
    so the path is more obvious when looking at tracks on printed board
    [SB Quick connect.kicad_pcb]
2022-11-06 v3 Fixes 🪲⚡
    Added missing track for A1.
    Moved PCF track further from mounting hole.
    Used correct footprint for LED bypass.
    [SB Quick connect.kicad_pcb]
2022-11-06 Rename KiCAD project files to CANburner
    [CANburner.csv, CANburner.kicad_pcb, CANburner.kicad_sch]
2022-11-12 add fanpcb from hartk
    [Drill_NPTH_Through.DRL, Drill_PTH_Through.DRL, Gerber_BoardOutlineLayer.GKO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]
2022-11-12 Rev 4 and fanpcb
    [FanPCB.kicad_pcb, FanPCB.kicad_sch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]
2022-11-12 rev 4 changes
    [SB Quick connect.csv, SB Quick connect.kicad_pcb]
2022-11-17 Fixed Net Trace on resistor for v4
    [SB Quick connect.kicad_pcb]
2022-11-18 Fixed solder mask logos over traces
    [SB Quick connect.kicad_pcb]
2022-11-20 CANBurner v4 Fabricated
    [SB Quick connect-B_Cu.gbr, SB Quick connect-B_Mask.gbr, SB Quick connect-B_Paste.gbr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]
2022-11-20 CANBurner v5
    [CANBurner-BOM.csv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]
2023-01-11 CANBurner v5 updates
    [CANBurner.step]
